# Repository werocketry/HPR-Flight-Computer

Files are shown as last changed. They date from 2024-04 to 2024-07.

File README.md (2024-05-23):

**Builds on [HPR Rocket Flight Computer](https://github.com/SparkyVT/HPR-Rocket-Flight-Computer) by SparkyVT**  

## DESCRIPTION

This flight computer is designed for rockets 38mm in diameter or greater, and will fit inside a 38mm tube coupler.  
**Dimensions**: 4.0in x 1.25in x 0.5in, antenna configuration may add more length  
It has similar capability as a TeleMega, but without a smart-phone app or advanced interfaces  
Flight-tested on multiple M-and-N powered supersonic flights to over 34K feet and Mach 2.3.  
For large or high-power projects, a commercially available backup computer is strongly recommended.  

## FEATURES

- Full-featured dual deploy/multi-stage/airstart rocket flight computer capable to 100,000ft or more
- Tilt-sensing lockout for ignition of second stages and/or airstarts
- Live telemetry over 433MHz or 915MHz LoRa (433MHz: USA amateur 70cm band, EUR license free) (915MHz: USA license free) 
- 4 high-current pyro outputs with continuity checks
- Advanced MEMS sensor package: GNSS, accelerometers, gyroscope, magnetometer, barometer, and LoRa radio
- High Data-Capture rate: approximately 50,000 samples per second recorded to SD card
  - 1000Hz 3-axis digital 24G and 100G accelerometer data logging
  - 1000Hz 3-axis digital 2000dps gyroscope data logging
  - 1000Hz of flight events & continuity data logging
  - 1000Hz of sensor-fuzed speed & altitude
  - 100Hz of pitch, yaw, roll rotation
  - 40Hz of magnetic data logging and magnetic roll
  - 30Hz-100Hz of digital barometric data logging (Altitude, pressure, temperature)
  - 30Hz of main battery voltage (1400Hz during pyro events)
  - 20Hz of LoRa telemetry output (time, event, acceleration, speed, altitude, rotation, GNSS position, signal strength)
  - 5Hz-25Hz of GNSS data logging (chip-dependent data rates & constellations)
  - Separate data file for each flight up to 100 flights
  - Optional separate GNSS NMEA capture file for plotting in Google Earth, UBLOX NEO-M9N configuration approved for TRA altitude record attempts
- Simple, easy-to-use configuration interface through the SD card
  - User Selectable Flight Mode: Single-Stage, Two-Stage, Airstart, or Booster
  - Configurable Apogee delay
  - Optional Audible Battery Voltage report at startup
  - Optional Magnetic Switch Startup & Shut-down
  - Preflight audible reporting options: Perfectflight or Marsa
  - User selectable telemetry frequency & power settings
  - 8 configurable servo outputs (4 powered, 4 un-powered)
  - User selectable inflight brownout recovery
- Mach immune, sensor-fusion based apogee event
- Barometric based main deploy event
- Audible pre-flight continuity report
- Audible Post-flight max altitude & speed report
- Mount in any orientation, automatic orientation detection with built-in self calibration mode
- Bench-test mode activated w/ tactile button; user configurable status messages over USB Serial
- Report in SI or Metric units
- Compatible with Teensy 3.2, 3.5, 3.6, 4.0, 4.1
  - Connect any sensor to any available I2C or SPI bus
  - Create your own custom setup with configurable pins for continuity, firing, and servos
  - Connect UBLOX GPS unit to any available HW Serial port

## FLIGHT COMPUTER COMPONENTS

- **Microprocessor**: Teensy 4.1, 3.5, or 3.6 (compatible with provided PCB file) or Teensy 4.0/3.2 (no PCB file provided)
- **IMU**: LSM6DS0X (recommended), LSM9DS1, LSM6DS33, MPU6050, or LSM303 & L3GD20H combo
- **Magnetometer**: LIS3MDL (recommended), LSM9DS1, or LSM303
- **100G Accelerometer**: H3LIS331DL (recommended), ADXL377, or ADXL377 & ADS1115 combo
- **Pressure Sensor**: MS5611 (recommended), MS5607, MPL3115A2, BMP180, BMP280, or BMP388 (Note: BMP280 & BMP388 incompatible with telemetry due to EMI)
- **GNSS**: UBLOX M6, M7, M8, M9 (NEO footprint supported in PCB file) or Adafruit Ultimate GPS
- **LoRa Telemetry**: RFM96W or RFM95W, both capable of TX on 433MHz or 915MHz (433MHz USA: Amateur License Required, EUR: License Free)

## GROUND STATION COMPONENTS

- **MCU**: Arduino Nano 33 BLE
- **Telemetry**: RFM96W 433MHz (USA: Ham License Required, EUR: License Free) or RFM95W 915MHz (USA: License Free)
- **GPS**: Ublox SAM-M8Q (optional)
- **IMU**: Sparkfun LSM9DS1 breakout
- **LCD**: 20X4 Sparkfun LCD
- **SD Card**: Adafruit SD Card breakout board
- **Antenna**: 433Mhz 5-element Yagi (Ham Only) or 900Mhz (License Free)

## ADDITIONAL LIBRARIES REQUIRED

- TinyGPS++
- SDfat and/or SD

## HARDWARE OPTIONS

- **OPTION 1**: Assemble the unit yourself. Purchase a Teensy 4.0 or 4.1 and integrate the system with commercially available sensor breakout boards. If you want to use high-current pyro outputs, then it is up to you to develop the continuity and firing circuitry. I have threaded standoffs and screws that are a perfect fit for the Adafruit breakout boards.
- **OPTION 2**: Contact me for a custom Teensy breakout board and add your own sensors. The breakout includes a Teensy 4.1, integrates 4x high-current pyro outputs, and 6 easy-to-use terminal blocks to integrate into your high-power rocket. Includes Qwiic connector to easily integrate your custom sensor package over I2C.
- **OPTION 3**: Contact me for a fully-functional Frankenstein-board. This integrates all sensors breakout boards onto a single main board that is 4.0 x 1.25 x 0.5 inches. Comes fully assembled, pre-programmed, calibrated, and tested. Configurations will vary, but quality will not.  
- **OPTION 4**: Try your hand at assembling the Frankenstein-board yourself. This is a single bare-board with no breakouts attached. You will need to reflow the GNSS chip and hand-solder approximately 30 components. Instructions included. Contact me for for a bare-board.
- **OPTION 5**: Contact me for a fully assembled and tested ground station. Includes ground unit with 2 radios and 20x4 LCD mounted in a custom form-fitting box.

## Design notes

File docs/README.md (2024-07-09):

# Welcome to the HPR-Flight-Computer Docs

## Operations Flow Chart

Source can be found on Cameron Brooks' Google Drive: [drive.google.com/file/d/1UoUj555KsNLJwYxSnVGjF17hvRSPmnp4/view?usp=drive_link](https://drive.google.com/file/d/1UoUj555KsNLJwYxSnVGjF17hvRSPmnp4/view?usp=drive_link)

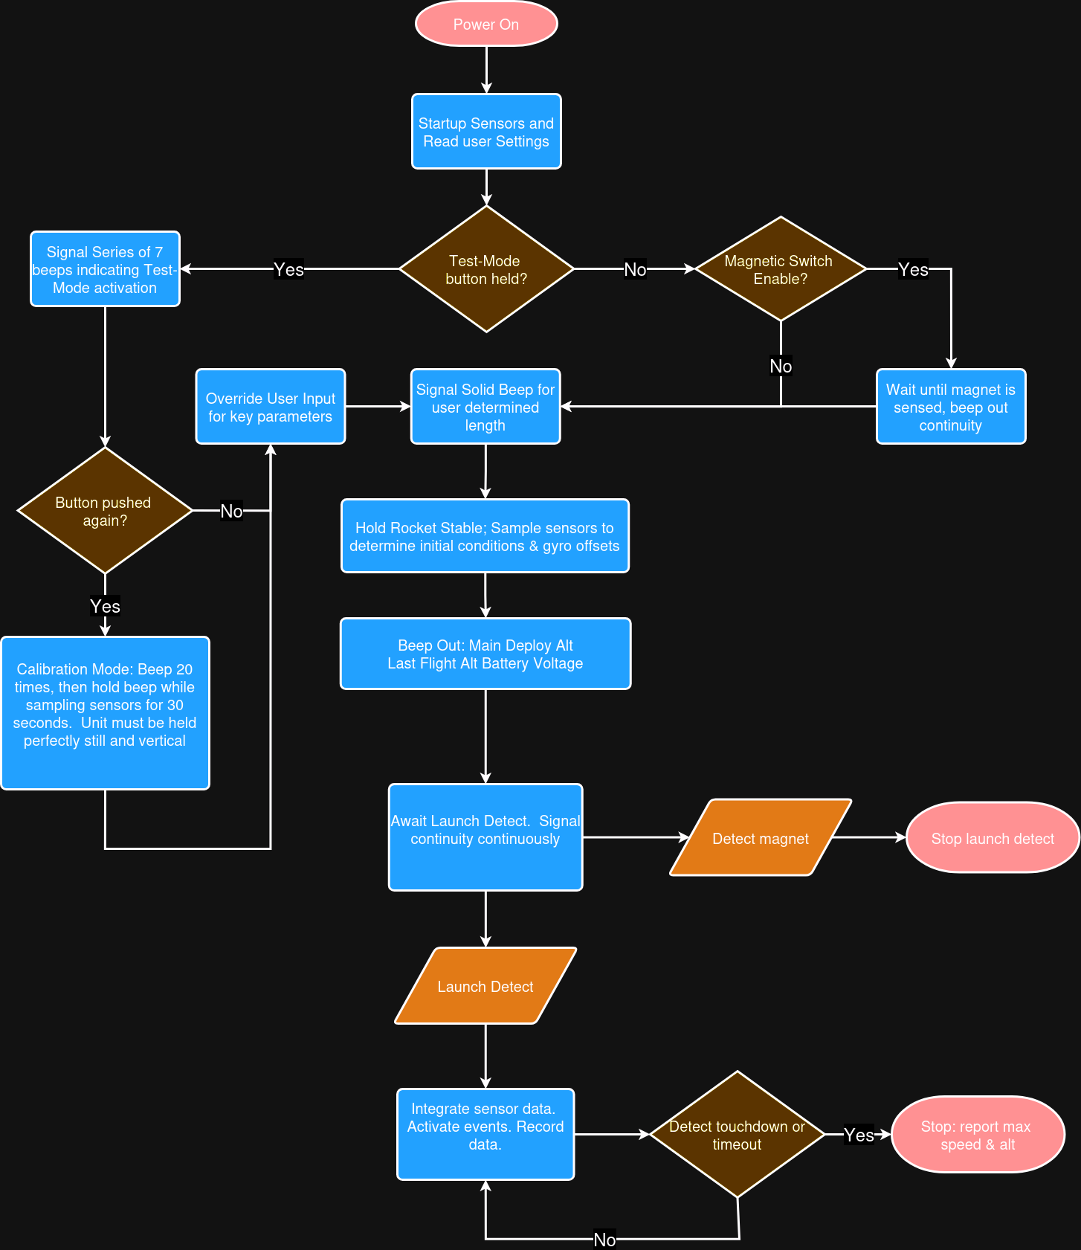
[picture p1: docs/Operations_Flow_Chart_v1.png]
Operations_Flow_Chart_v1


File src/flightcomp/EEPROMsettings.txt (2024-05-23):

EEPROM for version 4.7.0
Place this file into the root folder of the SD card
At startup the flight computer will read it and update the EEPROM
Once finished, the flight computer will delete this file
-----Device ID Code------
accel = 3
mag = 3
gyro = 3
highG = 0
baro = 7
radio = 1
GPS = 4
SD = 1
------Device Buses--------
accel = I0
mag = I0
gyro = I0
highG = S0
baro = I0
radio = S0
GPS = U1
SD = IO
----Sensor Orientation to Board----
accelX = +X
accelY = +Y
accelZ = +Z
gyroX = +X
gyroY = +Y
gyroZ = +Z
highGx = -X
highGy = +Y
highGz = +Z
magX = +X
magY = +Y
magZ = +Z
-------GPIO---------
pyro1cont = 14
pyro1fire = 39
pyro2cont = 16
pyro2fire = 15
pyro3cont = 26
pyro3fire = 17
pyro4cont = 22
pyro4fire = 27
nullPin = 56
beepPin = 23
battVoltPin = 33
testGnd = 2
testRead = 5
radioIRQ = 28
radioRST = 34
radioEN = 56
radioCS = 9
accelCS = 56
gyroCS = 56
highG-CS = 10
magCS = 56
baroCS = 56
sdCS = 56
----Servo Control Pins----
servo 1 pin = 6
servo 2 pin = 7
servo 3 pin = 20
servo 4 pin = 21
servo 5 pin = 38
servo 6 pin = 37
servo 7 pin = 36
servo 8 pin = 35
----Ham Radio Call Sign----
callSign = KK4ELF
-----Magnetometer-----
calibrateMode = 0
-----Hardware ID-----
HWid = 331
________________________________
Device ID Legend
________________________________
Accel: LSM303 = 1, LSM9DS1 = 2, LSM6DS33 = 3, MPU6050 = 4, External Library = 5
Gyro: none = 0, L3GD20H = 1, LSM9DS1 = 2, LSM6DS33 = 3, MPU6050 = 4, External Library = 5
Mag: none = 0, LSM303 = 1, LSM9DS1 = 2, LIS3MDL = 3, External Library = 4
highG: none = 0, ADS1115/ADXL377 combo = 1, H3LIS331DL = 2, TeensyADC/ADXL377 combo = 3, External Library = 4
baro: BMP180 = 1, MPL3115A2 = 2, BMP280 = 3, BMP388 = 4, MS5611 = 5, MS5607 = 6, LPS25H = 7, External Library = 8
GPS: none = 0, NEO-M8N = 1, SAM/MAX/NEO-M8Q/W = 2, NEO-M9N = 3, Adafruit Ultimate GPS or External Library = 4
radio: none = 0, Semtech SX1276/7/8/9 = 1, External Library = 2
SD: none = 0, SDcard present = 1
________________________________
Device Bus Legend
________________________________
I0: I2C bus0, SDA: 18, SCL: 19 (All Versions - default)
I1: I2C bus1, SDA: 37, SCL: 38 (Teensy 3.5/6 - default)
I1: I2C bus1, SDA: 30, SCL: 29 (Teensy 3.2   - default)
I1: I2C bus1, SDA: 17, SCL: 16 (Teensy 4.0/1 - default)
I2: I2C bus2, SDA: 03, SCL: 04 (Teensy 3.5/6 - default)
I2: I2C bus2, SDA: 25, SCL: 24 (Teensy 4.0/1 - default)
I3: I2C bus3, SDA: 56, SCL: 57 (Teensy 3.6   - default)
I4: I2C bus0, SDA: 17, SCL: 16 (Teensy 3.2/5/6 - altPins)
I5: I2C bus0, SDA: 07, SCL: 08 (Teensy 3.5/6 - altPins)
I6: I2C bus0, SDA: 34, SCL: 33 (Teensy 3.5/6 - altPins)
I7: I2C bus0, SDA: 48, SCL: 47 (Teensy 3.5/6 - altPins)
S0: SPI bus0, SCK: 13, MISO: 12, MOSI: 11 (All Versions)
S1: SPI bus1, SCK: 32, MISO:  1, MOSI:  0 (Teensy 3.5/6)
S1: SPI bus1, SCK: 27, MISO: 39, MOSI: 26 (Teensy 4.1)
S2: SPI bus2, SCK: 46, MISO: 45, MOSI: 44 (Teensy 3.5/6)
IO: SDIO default bus for Teensy 3.5, 3.6, 4.1
U1,U2,U3: Hardware Serial Bus (All Versions)
U4,U5,U6: Hardware Serial Bus Teensy 3.5/6/4.0/4.1
U7: Hardware Serial Bus Teensy 4.0/4.1
U8: Hardware Serial Bus Teensy 4.1
________________________________
Hardware ID (HWid) Legend
________________________________
1st digit: Generation
2nd digit: Revision
3rd digit: Unit#

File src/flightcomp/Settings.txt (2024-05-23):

Flight Computer Settings File
Not not delete or change the order of the settings
***********************
----Flight Settings----
***********************
Rocket Name = Mach Shock
flightProfile = S
units = S
reportStyle = P
startupTime = 10
mainDeployAlt = 700
apogeeDelay = 0.0
maxRecordTime = 900
silentTestMode = 1
magSwitchEnable = 0
inflightRecovery = 1
GPSlogFile = 0
***********************
-----Pyro Settings-----
***********************
pyroFiringTime = 0.5
pyro4function = M
pyro3function = A
pyro2function = N
pyro1function = N
***********************
--Telemetry Settings---
***********************
TXenable = 1
TXpwr = 13
TXfreq = 433.250
FHSS = 0
**********************************
---------2 Stage Settings---------
IGNORED UNLESS FLIGHT PROFILE IS 2
**********************************
boosterSeparationDelay = 0.5
sustainerIgnitionDelay = 0.5
**********************************
--------Airstart Settings---------
IGNORED UNLESS FLIGHT PROFILE IS A
**********************************
1stAirstartEvent = I
1stAirStartDelayTime = 0.5
2ndAirStartEvent = B
2ndAirStartDelayTime = 0.0
**************************************************
-----Safety Thresholds for Inflight Iginition-----
IGNORED UNLESS FLIGHT PROFILE IS 2 OR PROFILE IS A
**************************************************
altitudeThreshold = 400
maxAngleOffVertical = 20
***********************************
---Active Stabilization Settings---
***********************************
stableRotn = 0
stableVert = 0
************************************
---Fly-Back to Launchpad Settings---
************************************
FlyBack = 0
************************************
-----Serial Debugging Settings-----
************************************
serialDebug = 1
************************************************************************************************
                        valid setting values
************************************************************************************************
---------------------------------------------
         Flight Settings
---------------------------------------------
         Rocket Name: up to 20 characters of text
       flightProfile: S = single stage, 2 = 2-stage, A = Airstart, B = booster stage (single stage but recorded differently)
               units: S = US Standard System, M = Metric System  
         reportStyle: P = Perfectflite, M = Marsa
         startupTime: seconds from power-on until start of pre-flight sequence
       mainDeployAlt: altitude to deploy mains, 100ft to 1500ft (30m to 458m)
        apogee delay: # of seconds after apogee to fire charge, between 0.0 and 5.0
       maxRecordTime: if touchdown is not detected, recording will stop after this many seconds, between 300 and 4294
      silentTestMode: 1 enable, 0 disable, if enabled the audible beeper is silent during testMode
     magSwitchEnable: 1 enable, 0 disable, if enabled startup will not proceed until magnet is sensed.  Very useful for 2-stage mode.
    inflightRecovery: 0 - disabled, 1 - inflight brownout recovery w/out pyros, 2 - inflight brownout recovery with pyros
          GPSlogFile: 1 - saves all NMEA strings to a separate log file for TRA contest record attempts, 0 - no separate GPS log file
---------------------------------------------
         Telemetry Configuration
---------------------------------------------
          TXenable: 1 enable telemetry, 0 disable telemetry
             TXpwr: telemetry TX power; integers between 2 and 20; 13=20mW, 15=30mW, 17=50mW, 20=100mW
	      TXfreq: Radio frequency for 433MHz band or 915MHz band (power limit of 2mW on 915MHz band without FHSS)
	        FHSS: Frequency Hopping Spread Spectrum implementation for 915MHz ISM band (no FCC license required)
---------------------------------------------
         Pyro Channel Configuration
---------------------------------------------
  pyroFiringTime: total seconds spent sending current to pyro charge, between 0.2 and 1.0
   pyroFunctions: Any single character setting below is acceptable
		   M: Main deployment.  Fires when post-apogee altitude reaches mainDeployAlt 
		   A: Apogee deployment.  Fires on apogee detection with a delay of apogeeDelay seconds
		   I: 2-stage Mode - Sustainer ignition.  Fires 2-stage sustainer provided all saftey conditions are met.
		   B: 2-stage Mode - Booster separation.  Fires 1st stage separation charge on burnout detection with a delay of boosterSeparateDelay.
		   1: AirStart Mode - 1st AirStart.  Fires 1st Airstart after designated trigger event plus delay if safety conditions are met.
               2: AirStart Mode - 2nd AirStart.  Fires 2nd Airstart after designated trigger event plus delay if safety conditions are met.
               N: Pyro not used; no output funtion.  Nothing should be attached to the output.
---------------------------------------------
         2 Stage Rocket Settings
---------------------------------------------
 2stageIgnitionDelay: Fires 2nd stage this many seconds after booster separation, between 0.0 and 8.0
boosterSeparateDelay: Fires 1st stage separation charge this many seconds after booster burnout, between 0.0 and 3.0
---------------------------------------------
            Air Start Settings
---------------------------------------------
    1stAirstartEvent: I = starts delay timer upon main motor ignition, B = starts delay timer on main motor burnout
1stAirStartDelayTime: 1st Airstart pyro channel will fire this many seconds after the 1st Airstart Event
    2ndAirStartEvent: I = starts 2nd airstart timer upon 1st Airstart motor ignition, B = starts 2nd airstart timer on 1st Airstart motor burnout
2ndAirStartDelayTime: 2nd Airstart pyro channel will fire this many seconds after the 2nd Airstart Event
---------------------------------------------
     Inflight Ignition Safety Settings
---------------------------------------------
   altitudeThreshold: minimum altitude that must be exceeded before inflight ignition, 100ft (91m) minimum, no maximum
 maxAngleOffVertical: if angle off vertical exceeds this value then inflight igntion will not occur, between 0 and 90 degrees
---------------------------------------------
     Active Stabilization Settings
---------------------------------------------
	  stableRotn: 1 enable, 0 disable, the use of canard fins to correct the rocket rotation
	  stableVert: 1 enable, 0 disable, the use of canard fins to correct the rocket attitude and maintain vertical flight
---------------------------------------------
     Fly-Back to Launch Pad Settings
---------------------------------------------	
             flyBack: 1 enable, 0 disable, ability to guide the rocket back to the original launch site
---------------------------------------------
     Serial Debugging Settings
---------------------------------------------	
         serialDebug: 0 - no serial data after initial setup
         serialDebug: 1 - GPS data over serial in bench-test mode
         serialDebug: 2 - telemetry debugging data in bench-test mode
         serialDebug: 3 - GPS & telemetry debugging data in bench-test mode

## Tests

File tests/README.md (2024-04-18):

### `/tests`

Contains all unit tests for the library, will be organized to mirror the structure of the library itself.

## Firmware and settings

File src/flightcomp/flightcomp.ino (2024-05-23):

/**
 * @file hpr_flightcomp_V4_6_0.cpp
 * @brief High-Power Rocketry Flight Computer for Teensy 3.2, 3.5, 3.6, 4.0, and 4.1
 * 
 * Original sketch by Bryan Sparkman, TRA #12111, NAR #85720, L3
 * Modified and continued by Cameron K. Brooks
 * 
 *
 * @section features Features
 * - Dual-deploy flight computer capable to over 100,000ft
 * - Two-stage & airstart capable with tilt-sensing safety features
 * - Live telemetry over 433MHz or 915MHz LoRa 
 *   - 433MHz: USA amateur 70cm band, EUR license-free 
 *   - 915MHz: USA FHSS license-free or USA amateur license use non-FHSS
 * - 4 programmable high-current pyro outputs with continuity checks
 * - Captures high-rate data at approximately 50,000 data points per second on SD card
 *   - 1000Hz 3-axis digital 16G and 100G accelerometer data logging
 *   - 1000Hz 3-axis digital 2000dps gyroscope data logging
 *   - 1000Hz of flight events & continuity data logging
 *   - 1000Hz of sensor-fused speed & altitude
 *   - 100Hz of roll, pitch, yaw rotation
 *   - 40Hz of magnetic data logging and magnetic roll
 *   - 30Hz-100Hz of digital barometric data logging 
 *   - 30Hz of main battery voltage (1000Hz during pyro events)
 *   - 20Hz of LoRa telemetry output (time, event, acceleration, speed, altitude, rotation, GNSS altitude, GNSS position, signal strength, packet number)
 *   - 5Hz-25Hz of GNSS data logging (chip-dependent data rates & constellations)
 * - Separate data file for each flight (up to 100 flights)
 * - Simple, easy-to-use setup through the SD card
 *   - User Selectable Flight Mode: Single-Stage, Two-Stage, Airstart, or Booster
 *   - Configurable Apogee delay
 *   - Optional Audible Battery Voltage report at startup
 *   - Optional Magnetic Switch Startup & Shutdown
 *   - Preflight audible reporting options: Perfectflight or Marsa
 *   - User-selectable frequency & power settings for telemetry
 *   - 8 configurable servo outputs (4 powered, 4 unpowered)
 *   - User-selectable inflight brownout recovery
 *   - User-selectable active stabilization for roll, pitch, and yaw correction
 *   - User-selectable return-to-pad controlled recovery
 * - Tilt-sensing lockout for ignition of second stages and/or airstarts
 * - Mach immune, sensor-fusion based apogee event
 * - Barometric-based main deploy event
 * - Optional GNSS NMEA Log for TRA altitude contest reporting
 * - Audible pre-flight continuity report
 * - Audible Post-flight max altitude & speed report
 * - Mount in any orientation with automatic orientation detection during calibration
 * - Bench-test mode activated with tactile button
 * - Built-in self-calibration mode
 * - Report in SI or Metric units
 * - Compatible with Teensy 3.2, 3.5, 3.6, 4.0, 4.1
 *   - Compatible with many different sensors over I2C or SPI
 *   - GPS can be wired to any available HW Serial port (Ublox M6, M7, M8, M9 supported)
 *
 * @section changelog Change Log
 * - V4_0_0 combines all previous versions coded for specific hardware setups
 * - V4_1_0 adds upgrades for airstart capability, more flight event codes, improved settings file, PWM Pyro firing, quaternion rotation
 * - V4_1_1 eliminates timer interrupts, improves telemetry timing, enables the Galileo GNSS system
 * - V4_1_2 increases the GPS data rates and fixes some bugs in the pyro firing timing
 * - V4_1_3 adds features to the settings file, moves some settings to the EEPROM file, adds calibration for the MPL3115A2
 * - V4_1_4 adds magnetic rotation and increases the magnetic data capture rate
 * - V4_2_0 adds 915MHz FHSS telemetry capability, configurable GNSS & radio debugging
 * - V4_2_2 adds support for the MS5611 pressure sensor
 * - V4_2_3 adds inflight recovery from brown-out or MCU reset, sensor fusion altitude and velocity, eliminates gyro high-pass filter
 * - V4_3_0 updates Quaternion rotation for the best possible precision, corrects some GNSS bugs
 * - V4_3_1 makes FHSS an option on 915MHz and corrects some bugs in the FHSS power settings code
 * - V4_3_2 fixes bugs in the orientation & rotation routines, forces inline functions for faster execution, fixes multiple bugs picked up by the new Arduino compiler
 * - V4_3_3 creates a user interface over serial to calibrate the barometer, extends gyro orientation integration through the entire flight
 * - V4_3_4 enables active stabilization, creates basic fin trim code, and enables auto-adjusting gain on the IMU accelerometer
 * - V4_3_5 removes auto-adjusting gain, improves calibration routines, extends baro calibration to all sensors, removed high-G axis mode from user settings
 * - V4_3_6 adds return-to-base functionality (beta testing), supports LSM6DS33, LIS3MDL, and MS5607, updates code for separate mag sensors
 * - V4_4_0 creates flexible I2C and SPI bus routines for various devices and buses across Teensy3.X and Teensy4.X platforms
 * - V4_4_2 further streamlines the bus management functions with more efficient pointers, overclocks I2C speed on some sensors, implements controlled sampling of all sensors, continuously checks pre-flight continuity, improved barometric smoothing
 * - V4_5_0 eliminates RadioHead library due to interferences with the PWMServo library, now uses an interval timer for precise control of the radio packet timing
 * - V4_5_1 adds optional GPS output file to capture NMEA sentences for contest flights, creates better radio resiliency by adding the callsign back into the header of the packet
 * - V4_5_2 finishes the draft RTB code, adds a canard calibration flight mode, fixed GPS bug with NEO-M8N
 * - V4_5_3 uses the RFM96W in both 70cm and 900MHz mode based on user frequency input for 3 options
 * - V4_5_4 fixes a bug in the sensor timing that reduced the effective data capture rate
 * - V4_5_5 removes launch detection user options since the algorithm is proven reliable, fixes a timing bug with the barometers, makes GPS configuration code more portable, adds LPS25H support, fixes bugs with LSM6DS33 and LIS3MDL
 * - V4_6_0 improves portability of quaternion rotation code, adds MPU6050 support, fixed calibration routine bug, cleaned up some of the GPS data processing, corrected major bug in high-G moving average
 *
 * @section future_upgrades Future Upgrades
 * - Active Stabilization (started)
 * - Return-to-Base capability (started)
 * - 3D position physics model
 * - Remote Arm & Shutdown Commands over LoRa
 * - Ground Station Bluetooth Datalink to smartphone (started)
 * - Smartphone App
 *
 * @section todo To-Do List
 * - Finish bench testing of inflight recovery routines
 * - Flight test airstart code
 * - Debug inflight recovery
 * - Stuck-in-a-loop detection and breakout
 */



//-------CODE START--------
#include <EEPROM.h>
#include <TinyGPS++.h>
#include <PWMServo.h>
#include <SPI.h>
// Teensy 3.X
#if defined(__MK64FX512__) || defined(__MK66FX1M0__) || defined(__MK20DX256__)
// i2c_t3 is needed to enable the different pin options of bus0
#include <i2c_t3.h>
// NOTE: typedef declarations must be in the main file and not the tabs
typedef i2c_t3 TwoWire;
#endif
// Teensy 4.X
#if defined(__IMXRT1062__)
#include <Wire.h>
#endif

// Hardware Serial for GPS
HardwareSerial *HWSERIAL;

// GPS Setup
TinyGPSPlus GPS;

// Servo Setup
PWMServo canardYaw1;
PWMServo canardYaw2;
PWMServo canardPitch3;
PWMServo canardPitch4;
PWMServo actionServo5;
PWMServo actionServo6;
PWMServo actionServo7;
PWMServo actionServo8;

// Timer for the radio
IntervalTimer radioTimer;
IntervalTimer syncTimer;
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
void loop(void)
{

  // debug
  if (settings.testMode)
  {
    sampleStart = micros();
  }

  // Check if an accelerometer sample is needed and set timestamp
  fltTime.tmClock = sampleTimeCheck = micros();
  if (sampleTimeCheck - accel.timeLastSamp > accel.timeBtwnSamp)
  {
    getAccel();
    accel.timeLastSamp += accel.timeBtwnSamp;
    while (sampleTimeCheck - accel.timeLastSamp > accel.timeBtwnSamp)
    {
      accel.timeLastSamp += accel.timeBtwnSamp;
    }
  }

  // Check if an gyroscope sample is needed
  sampleTimeCheck = micros();
  if (sampleTimeCheck - gyro.timeLastSamp > gyro.timeBtwnSamp)
  {
    getGyro();
    gyro.timeLastSamp += gyro.timeBtwnSamp;
    while (sampleTimeCheck - gyro.timeLastSamp > gyro.timeBtwnSamp)
    {
      gyro.timeLastSamp += gyro.timeBtwnSamp;
    }
  }

  // Check if a high-G accelerometer sample is needed
  sampleTimeCheck = micros();
  if (sampleTimeCheck - highG.timeLastSamp > highG.timeBtwnSamp)
  {
    getHighG();
    highG.timeLastSamp += highG.timeBtwnSamp;
    while (sampleTimeCheck - highG.timeLastSamp > highG.timeBtwnSamp)
    {
      highG.timeLastSamp += highG.timeBtwnSamp;
    }
  }

  // Check if a barometer sample is needed
  sampleTimeCheck = micros();
  if (sampleTimeCheck - baro.timeLastSamp > baro.timeBtwnSamp)
  {
    getBaro();
    // barometers work in single-shot mode so we can't use time-block sampling like the other sensors
    baro.timeLastSamp = sampleTimeCheck;
  }

  // Check if a magnetometer sample is needed
  sampleTimeCheck = micros();
  if (sampleTimeCheck - mag.timeLastSamp > mag.timeBtwnSamp)
  {
    getMag();
    mag.timeLastSamp += mag.timeBtwnSamp;
    while (sampleTimeCheck - mag.timeLastSamp > mag.timeBtwnSamp)
    {
      mag.timeLastSamp += mag.timeBtwnSamp;
    }
  }

  // Sample continuity
  checkPyroContinuity();

  // debug
  if (settings.testMode)
  {
    sampleTime = micros() - sampleStart;
  }

  // process barometric samples
  // See if a new altitude reading is available
  if (baro.newSamp)
  {
    processBaroSamp();
  }

  // look for a shutdown command and if seen, stop all progress for a hard reset
  if (events.preLiftoff && settings.magSwitchEnable)
  {
    getMag();
    n = 0;
    if (abs(mag.x) > magTrigger || abs(mag.y) > magTrigger || abs(mag.z) > magTrigger)
    {
      n = 1;
    }
    while (n == 1)
    {
      digitalWrite(pins.beep, HIGH);
      delay(1000);
    }
  }

  // detect liftoff
  if (!events.liftoff && accel.z > gTrigger && !events.touchdown && !events.timeOut)
  {
    if (settings.testMode)
    {
      Serial.println(' ');
      Serial.println(F("Simulated Liftoff Detected!"));
    }
    fltTime.padTime = fltTime.tmClockPrev = fltTime.tmClock;
    events.preLiftoff = false;
    events.liftoff = true;
    events.inFlight = true;
    fltTime.liftoff = fltTime.tmClock;
    radio.event = Liftoff;
    radio.alt = 0;
    radioTimer.begin(timerSendPkt, pktInterval.inflight);
    noInterrupts();
    sendPkt = true;
    interrupts();
    gnss.liftoff.hour = GPS.time.hour();
    gnss.liftoff.minute = GPS.time.minute();
    gnss.liftoff.second = GPS.time.second();
    gnss.liftoff.mili = GPS.time.centisecond();
    gnss.maxAlt = 0.0F;
    // store base alt in EEPROM
    floatUnion.val = baro.baseAlt;
    if (settings.inflightRecover != 0)
    {
      for (byte i = 0; i < 4; i++)
      {
        EEPROM.update(eeprom.baseAlt + i, floatUnion.Byte[i]);
      }
      EEPROM.update(eeprom.lastEvent, radio.event);
    }
  }

  if (events.liftoff)
  {

    // capture the cycles between samples
    if (settings.testMode)
    {
      cyclesBtwn++;
    }

    // set cycle timestamp
    fltTime.dt = fltTime.tmClock - fltTime.tmClockPrev;
    fltTime.timeCurrent += fltTime.dt;
    fltTime.tmClockPrev = fltTime.tmClock;

    // Update the moving average which greatly improves accuracy with minimal latency
    if (highG.newSamp)
    {
      highGsum -= highGfilter[filterPosn];
      highGfilter[filterPosn] = highG.z;
      highGsum += highGfilter[filterPosn];
      filterPosn++;
      if (filterPosn >= sizeHighGfilter)
      {
        filterPosn = 0;
        if (!filterFull)
        {
          filterFull = true;
        }
      }
      if (!filterFull)
      {
        highGsmooth = highGsum / filterPosn;
      }
      else
      {
        highGsmooth = highGsum / sizeHighGfilter;
      }
    }

    // Compute the current g-load. Use the high-G accelerometer if the IMU is pegged and a high-G accelerometer is present
    if (abs(accel.z) < accel.ADCmax)
    {
      accelNow = (float)(accel.z - g) * accel.gainZ;
    }
    else if (!sensors.status_NoHighGAccel)
    {
      accelNow = (highG.z - (float)high1G) * highG.gainZ;
    }
    else
    {
      accelNow = (float)(accel.z - g) * accel.gainZ;
    }

    // Integrate velocity and altitude data prior to apogee
    if (!events.apogeeFire)
    {

      // Capture the max acceleration
      if (accelNow > maxG)
      {
        maxG = accelNow;
      }

      // calculate the new acceleration based velocity
      // this makes the apogee event mach immune
      accelVel += accelNow * (float)fltTime.dt * mlnth;

      // calculate the new acceleration based altitude
      accelAlt += accelVel * (float)fltTime.dt * mlnth;

      // calculate the new sensor fusion based velocity
      fusionVel += accelNow * (float)fltTime.dt * mlnth;
      // if we have a barometric update and its within acceptable flight parameters, then update the fusion algorithms
      bool updateFusionBaro = false;
      if (baro.newSamp && baro.Vel < 300 && baro.Vel < baro.maxVel && accelNow < 0.2F && fusionVel < 300.0F && baro.Alt < 13000)
      {
        updateFusionBaro = true;
      }
      if (updateFusionBaro)
      {
        fusionVel *= 0.99F;
        fusionVel += 0.01F * baro.Vel;
      }
      radio.vel = (int16_t)fusionVel;

      // update maximum velocity if it exceeds the previous value
      if (fusionVel > maxVelocity)
      {
        maxVelocity = fusionVel;
      }

      // calculate the new sensor fusion based altitude
      fusionAlt += fusionVel * (float)fltTime.dt * mlnth;
      if (updateFusionBaro)
      {
        fusionAlt *= 0.95;
        fusionAlt += 0.05 * baro.Alt;
        updateFusionBaro = false;
      }
      if (!altOK && (fusionAlt > settings.altThreshold || settings.testMode))
      {
        altOK = true;
      }
      radio.alt = (int16_t)fusionAlt;

    } // end if !apogee

    // caluclate the partial rotation
    dx += gyro.x * fltTime.dt;
    dy += gyro.y * fltTime.dt;
    dz += gyro.z * fltTime.dt;

    // if active stablization is on, then use the more stable rotation algorithm
    if (settings.stableRotn || settings.stableVert)
    {
      getDCM2DRotn(dx, dy, dz, gyro.gainZ);
      dx = dy = dz = 0L;
    }

    // update the quaternion rotation if we are not using active stabilization
    else if (fltTime.timeCurrent - lastRotn > rotnRate)
    {
      getQuatRotn(dx, dy, dz, gyro.gainZ);
      dx = dy = dz = 0L;
      lastRotn = fltTime.timeCurrent;
    }

    // run event logic
    checkEvents();

    // update the canards throws if stabilization or flyback is enabled
    if (settings.stableRotn || settings.stableVert || settings.flyBack)
    {
      uint32_t controlTime = micros();
      if (controlTime - timeLastControl >= controlInterval)
      {
        // if active stabilization is activated, set the canards
        if ((settings.stableVert || settings.stableRotn) && !events.apogee && events.boosterBurnout)
        {
          setCanards();
        }
        // if RTB is on and we are post apogee, then set canards to return to launch point
        if (settings.flyBack && events.apogeeFire && !events.mainDeploy)
        {
          setRTB();
        }
        // update control timer
        timeLastControl = controlTime;
      }
    }

    // Read the battery voltage
    if ((fltTime.timeCurrent - lastVolt > voltRate) || pyroFire)
    {
      voltReading = analogRead(pins.batt);
      voltage = (float)(voltReading) * 3.3 * 3.2 * adcConvert;
      if (pins.batt == pins.pyro4Cont)
      {
        voltage *= (2.72 / 3.2);
      } // on old units we used to pull the battery voltage through one of the pyro channels which had diodes
      writeVolt = true;
      lastVolt = fltTime.timeCurrent;
    }

    // Write the data to a string if we have a new sample
    if (accel.newSamp || gyro.newSamp || highG.newSamp || mag.newSamp || baro.newSamp || baro.newTemp || gnss.SDwrite || writeVolt || SDradioTX)
    {
      writeSDflightData();
    }
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

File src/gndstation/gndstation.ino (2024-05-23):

/**
 * @brief File: Telemetry_Rx_V10_Teensy.ino
 * 
 * This file contains the setup and loop functions for the rocket's control system.
 * 
 * Versions:
 * - V7 uses only a single microprocessor
 * - V8 uses an optimized data stream
 * - V9 overhauls the whole system
 * - V10 eliminates the RadioHead library
 * 
 * TO DO:
 * 0) Read user data from SD card
 * 1) Create BLE Service
 * 2) Pin correction for LCD - OK
 * 3) Radio 1 controls - OK
 * 4) Radio 2 controls - OK
 * 5) GPS Services - OK
 * 6) LSM9DS1 orientation
 * 7) LSM9DS1 magnetic
 * 8) Include Software SPI - OK
 * 9) Create user menu interface
 * 10) Delineate FHSS with a booster
 */

#include <SdFat.h>
#include <SerLCD.h>
#include <TinyGPS++.h>
#include <EEPROM.h>
#include <SPI.h>
#include <Wire.h>

//Hardware Serial for GPS
HardwareSerial *HWSERIAL;

//Radio control pins
#define radio1RST     14//ok
#define radio1CS      15//ok
#define radio1IRQ     17//ok
#define radio2RST     16//ok
#define radio2CS      20//ok
#define radio2IRQ     22//ok

//void preflightPacket(byte dataPacket[]);
//void inflightPacket(byte dataPacket[]);
//void postflightPacket(byte dataPacket[]);

char serialBuffer[256];
int serialPosn = 0;

byte dataPkt[80];
volatile boolean processIRQ = false;
uint32_t timeLastPkt = 0UL;
uint32_t debugTime;
int16_t pktRssi;
float radio1Freq = 433.500;
float radio2Freq = 433.250;

//RegOpMode
enum {
  SleepMode     =  0x00,
  StandbyMode   =  0x01,
  TXmode        =  0x03,
  RXmode        =  0x05,
  CADmode       =  0x07,
  LoRaMode      =  0x80, 
  LowFrqMode    =  0x08, //LowFrq mode enables registers below 860MHz
  writeMask     =  0x80};

byte radio1Fnctn = RXmode;
byte radio2Fnctn = RXmode;

const uint8_t SOFT_MISO_PIN  = 2;
const uint8_t SOFT_MOSI_PIN  = 1;
const uint8_t SOFT_SCK_PIN   = 3;
const uint8_t SD_CS_PIN      = 0; 

// SdFat software SPI template
SoftSpiDriver<SOFT_MISO_PIN, SOFT_MOSI_PIN, SOFT_SCK_PIN> softSpi;
#define SD_CONFIG SdSpiConfig(SD_CS_PIN, DEDICATED_SPI, SD_SCK_MHZ(0), &softSpi)

SdFs SD;
FsFile sustainerFile;
FsFile boosterFile;

//LCD Setup
SerLCD lcd;

// GPS Setup
TinyGPSPlus GPS;

//---------------------------
//Code Control Option variables
//---------------------------
boolean displayStandard = true;
boolean FHSS = false;
boolean debugSerial = true;
float unitConvert = 3.28084F;
boolean LCD = true;
boolean GPSdebug = false;
//---------------------------
//Data Packet variables
//---------------------------
uint8_t len;
byte dataPacket1[66];
byte dataPacket2[66];
char dataString[256];
boolean SDstatus = false;
char sustainerFileName[13] = "FLIGHT01.txt";
char boosterFileName[14] = "BOOSTER01.txt";
boolean sustainerFileOpen = false;
boolean boosterFileOpen = false;
boolean sustainerFileCreated = false;
boolean boosterFileCreated = false;
byte n = 0;
byte fileNum = 1;
byte pktPosn = 0;
int16_t packetnum = 0;
unsigned long timer = 0UL;
boolean radio1status = false;
boolean radio2status = false;
boolean sendPacket = true;
boolean testMode = false;
unsigned long testStart = 0UL;
unsigned long lastRX = 0UL;
unsigned long debugStart = 0UL;
unsigned long debugStop = 0UL;
unsigned long colorStart;
int battVolt;
boolean SDinit = false;
boolean LCDinit = true;
boolean parseSustainer = false;
boolean parseBooster = false;
uint32_t timeLastNMEA = 0UL;
bool ledLight = false;
//---------------------------
//preflight output variables
//---------------------------
uint8_t event;
int strPosn = 0;
boolean signalEst = false;
boolean dataProcessed = false;
boolean sustainerPreFlightWrite = true;
boolean boosterPreFlightWrite = true;
boolean sustainerPostFlightWrite = true;
boolean boosterPostFlightWrite = true;
boolean boosterFileReady = false;
unsigned long lostSignalTime = 2000000UL;
byte j=0;
//---------------------------
//preflight output variables
//---------------------------
char rocketName[20]="";
int baseAlt=0;
int baseGPSalt = 0;
byte contCode;
int satNum = 0;
boolean fileOpen = true;
//---------------------------
//inflight output variables
//---------------------------
uint16_t sampleTime;
int16_t signalStrength=0;
int16_t velocity = 0;
int16_t Alt=0;
int16_t spin=0;
int16_t offVert=0;
int16_t accel=0;
int16_t packetNum = 0;
boolean apogee = false;
unsigned long lastSustainerRX = 0UL;
unsigned long lastBoosterRX = 0UL;
//---------------------------
//Postflight output variables
//---------------------------
int maxAltitude=0;
int maxVelocity=0;
int maxG=0;
int maxGPSalt=0;
//GPS output variables
byte GPSlock;
int GPSalt=0;
int prevGPSalt;
char charGPSlat;
float GPSlatitude;
char charGPSlon;
float GPSlongitude;
float lastGPSlat;
float lastGPSlon;
float prevGPSlat = 0.0;
float prevGPSlon = 0.0;
unsigned long lastGPSfix = 0UL;
//---------------------------
//Radio Variables
//---------------------------
volatile boolean radio1Pkt = false;
volatile boolean radio2Pkt = false;
union {
   float GPScoord;
   unsigned long radioTime;
   byte unionByte[4];
} radioUnion;
union {
   int16_t unionInt;
   byte unionByte[2]; 
} radioInt;
byte chnl1 = 0;
byte chnl2 = 0;
byte hailChnl_1 = 0;
byte hailChnl_2 = 0;
byte nextChnl;
byte nextChnl2;
boolean syncFreq = false;
float freq1;
float freq2;
unsigned long lastHopTime = 0UL;
byte chnlUsed = 0;
boolean band433 = false;
byte radioFnctn;
//---------------------------
//LCD Variables
//---------------------------
byte whiteIntensity = 125;
byte redIntensity = 255;
byte greenIntensity = 255;
byte blueIntensity = 255;
byte flightPhase = 0;
//---------------------------
//BlueTooth Variables
//---------------------------
boolean blueTooth = true;
//---------------------------
//Event Table
//---------------------------
const String event_00 = "Preflight";
const String event_01 = "Liftoff";
const String event_02 = "Booster Burnout";
const String event_03 = "Apogee Detected";
const String event_04 = "Firing Apogee Pyro";
const String event_05 = "Separation Detected!";
const String event_06 = "Firing Mains";
const String event_07 = "Under Chute";
const String event_08 = "Ejecting Booster";
const String event_09 = "Firing 2nd Stage";
const String event_10 = "2nd Stage Ignition";
const String event_11 = "2nd Stage Burnout";
const String event_12 = "Firing Airstart1";
const String event_13 = "Airstart1 Ignition";
const String event_14 = "Airstart1 Burnout";
const String event_15 = "Firing Airstart2";
const String event_16 = "Airstart2 Ignition";
const String event_17 = "Airstart2 Burnout";
const String event_18 = "NoFire: Rotn Limit";
const String event_19 = "NoFire: Alt Limit";
const String event_20 = "NoFire: Rotn/Alt Lmt";
const String event_21 = "Booster Apogee";
const String event_22 = "Booster Apogee Fire";
const String event_23 = "Booster Separation!";
const String event_24 = "Booster Main Deploy";
const String event_25 = "Booster Under Chute";
const String event_26 = "Time Limit Exceeded";
const String event_27 = "Touchdown!";
const String event_28 = "Power Loss! Restart!";
const String event_29 = "Booster Touchdown!";
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

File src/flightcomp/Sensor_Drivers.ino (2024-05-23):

/**
 * @file Sensor_Drivers.ino
 * @brief Functions and routines for managing sensor drivers in Teensy-based projects.
 *
 * @details
 * This file contains various functions for starting and retrieving data from different sensors,
 * including accelerometers, gyroscopes, magnetometers, high-G accelerometers, and barometric sensors.
 * It supports multiple sensor models, offering generic functions for starting and retrieving data,
 * as well as sensor-specific routines for advanced operations.
 *
 * @section changelog Change Log
 * - 26 Nov 17: Version 1 created to support Adafruit 10Dof board.
 * - 10 Nov 18: Version 2 created to support LSM9DS1, H3LIS331DL, BMP280, BMP388.
 * - 30 Apr 19: Version 3 created to support MPL3115A2 after EMI problems with BMP280 and BMP388.
 * - 31 Jan 20: Version 4 created to support all coded sensors and all orientations.
 * - 29 Oct 20: Added code for MS5611 sensor.
 * - 04 Aug 21: Added variable gain for LSM9DS1 accelerometer.
 * - 10 Aug 21: Removed variable gain after testing showed no expected improvement.
 * - 12 Nov 21: Corrected MS5611 bugs and added SPI support for H3LIS331DL.
 * - 28 Nov 21: Extended generic barometric pressure sensor offset calibration to all supported sensors.
 * - 30 Dec 21: Added support for LSM6DS33, LIS3MDL, MS5607.
 * - 03 Jan 22: Moved I2C and SPI generic functions to Bus_Mgmt tab to better support different processors.
 * - 10 May 22: Updated to have any device on any I2C or SPI bus.
 * - 16 Jun 22: Updated with streamlined bus management functions, eliminated high-G 3-axis mode due to improved I2C speed.
 * - 13 Jun 23: Updated to add LPS25H support and correct bugs in LSM6DS33 and LIS3MDL.
 * - 13 Aug 23: Added MPU6050 support, eliminated redundant routines.
 *
 * @section supported_sensors Supported Sensors
 * - Accelerometers: LSM303, LSM9DS1, LSM6DS33
 * - Gyroscopes: L3GD20H, LSM9DS1, LSM6DS33
 * - Magnetometers: LSM303, LSM9DS1, LIS3MDL
 * - High-G Accelerometers: H3LIS331DL, ADS1115 & ADXL377 Combo, ADXL377 & Teensy3.5 ADC combo
 * - Barometric: BMP180, BMP280, BMP388, MPL3115A2, MS5611, MS5607, LPS25H
 *
 * @warning Some Bosch sensors, such as BMP280 and BMP388, may be sensitive to RF interference.
 *
 * @section generic_sensor_functions Generic Sensor Functions
 * - beginAccel(): Starts accelerometer.
 * - getAccel(): Gets accelerometer data.
 * - beginGyro(): Starts gyroscope.
 * - getGyro(): Gets gyroscope data.
 * - beginHighG(): Starts high-G accelerometer.
 * - getHighG(): Gets high-G accelerometer data.
 * - beginMag(): Starts magnetometer if external to IMU.
 * - resetMagGain(): Sets the magnetometer gain to 8 Gauss for the magnetic switch function.
 * - getMag(): Gets magnetometer data.
 * - beginBaro(): Starts the barometer.
 * - getBaro(): Gets the barometer data.
 *
 * @section sensor_specific_functions Sensor-Specific Functions
 * - beginLSM303_A(): Starts LSM303 accelerometer.
 * - beginLSM303_M(): Starts LSM303 magnetometer.
 * - getLSM303_A(): Gets LSM303 accelerometer data.
 * - getLSM303_M(): Gets LSM303 magnetometer data.
 *
 * - beginL3GD20H(): Starts L3GD20H gyroscope.
 * - getL3GS20H(): Gets L3GD20H gyroscope data.
 *
 * - beginLSM9DS1_AG(): Starts LSM9DS1 accelerometer & gyro.
 * - beginLSM9DS1_M(): Starts LSM9DS1 magnetometer.
 * - getLSM9DS1_AG(): Gets LSM9DS1 accelerometer & gyro data.
 * - getLSM9DS1_M(): Gets LSM9DS1 magnetometer data.
 *
 * - beginLSM6DS33(): Starts LSM6DS33 sensor.
 * - getLSM6DS33(): Gets LSM6DS33 accelerometer & gyro data.
 *
 * - beginMPU6050(): Starts MPU6050 sensor.
 * - getMPU6050_AG(): Gets MPU6050 accelerometer & gyro data.
 *
 * - beginLIS3MDL(): Starts LIS3MDL magnetometer.
 * - getLIS3MDL(): Gets LIS3MDL magnetometer data.
 *
 * - beginH3LIS331DL(): Starts H3LIS331DL high-G accelerometer.
 * - getH3LIS331DL(): Gets H3LIS331DL high-G accelerometer data.
 *
 * - beginADS1115(): Starts ADS1115 ADC.
 * - getADS1115(): Gets accelerometer data from ADXL377.
 * - writeRegister(): Helper function for ADS1115.
 *
 * - beginADXL377(): Starts Teensy ADC.
 * - getADXL377(): Gets accelerometer data from Teensy ADC.
 *
 * - beginBMP180(): Starts BMP180 barometric sensor.
 * - initiateTemp(): Initiates temperature measurement.
 * - initiatePressure(): Initiates pressure measurement.
 * - getPressure(): Retrieves pressure data.
 *
 * - beginBMP280(): Starts BMP280 sensor.
 * - readBMP280coefficients(): Reads BMP280 sensor calibration data.
 * - getBMP280(): Gets BMP280 sensor data.
 *
 * - beginBMP388(): Starts BMP388 sensor.
 * - readBMP388coefficients(): Reads BMP388 sensor calibration data.
 * - getBMP388(): Gets BMP388 sensor data.
 *
 * - beginMPL3115A2(): Starts MPL3115A2 sensor.
 * - getMPL3115A2(): Reads MPL3115A2 sensor data.
 * - pressureToAltitude(): Converts pressure to altitude.
 *
 * - beginMS56XX(): Starts MS56XX sensor.
 * - readPromMS56XX(): Reads MS56XX calibration settings from PROM.
 * - getMS56XX(): Retrieves MS56XX sensor data.
 * - readMS56XX(): Manages I2C bus speed.
 * - CmdMS56XX(): Helper function for sending commands.
 * - ConvertTempMS56XX(): Converts temperature.
 * - ConvertPressMS56XX(): Converts pressure.
 *
 * - beginLPS25H(): Starts LPS25H sensor.
 * - getLPS25H(): Gets both temperature and pressure data.
 */

//***************************************************************************
// Generic Sensor Begin & Read Statements
//***************************************************************************
/*!
 * @brief Initializes the appropriate accelerometer based on the configured sensor type.
 */
void beginAccel()
{

  switch (sensors.accel)
  {

  case 2:
    sensors.status_LSM9DS1 = beginLSM9DS1_AG();
    break;

  case 3:
    sensors.status_LSM6DS33 = beginLSM6DS33();
    break;

  case 1:
    sensors.status_LSM303 = beginLSM303_A();
    break;

  case 4:
    sensors.status_MPU6050 = beginMPU6050();
    break;
  }
} // end beginAccel

/*!
 * @brief Reads data from the appropriate accelerometer based on the configured sensor type.
 */
void getAccel()
{

  // get the sensor data
  switch (sensors.accel)
  {

  case 2:
    getLSM9DS1_AG();
    break;

  case 3:
    getLSM6DS33();
    break;

  case 1:
    getLSM303_A();
    break;

  case 4:
    getMPU6050();
    break;
  }

  // indicate new sample
  accel.newSamp = true;

  // remove bias
  accel.rawX -= accel.biasX;
  accel.rawY -= accel.biasY;
  accel.rawZ -= accel.biasZ;

  // orient sensor data
  accel.x = *accel.ptrX * *accel.ptrXsign;
  accel.y = *accel.ptrY * *accel.ptrYsign;
  accel.z = *accel.ptrZ * *accel.ptrZsign;
} // end getAccel

/*!
 * @brief Initializes the appropriate magnetometer based on the configured sensor type.
 */
void beginMag()
{

  switch (sensors.mag)
  {

  case 1:
    beginLSM303_M();
    break;

  case 2:
    beginLSM9DS1_M();
    break;

  case 3:
    beginLIS3MDL();
    break;

  default:
    break;
  }
} // end beginMag
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

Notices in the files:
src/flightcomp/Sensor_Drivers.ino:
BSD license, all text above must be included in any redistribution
